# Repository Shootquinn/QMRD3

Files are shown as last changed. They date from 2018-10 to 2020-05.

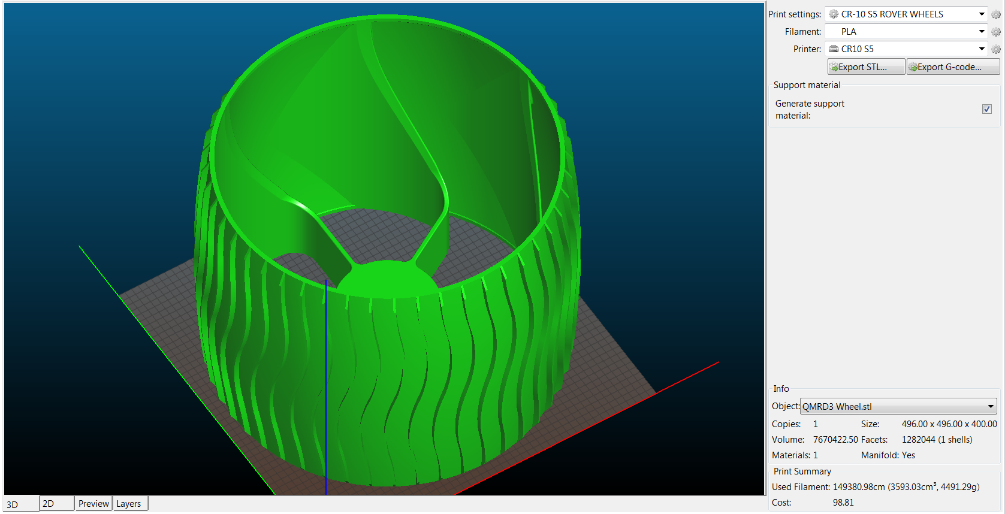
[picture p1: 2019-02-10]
QMRD3 Wheel Print Info Stock CR10S5.PNG

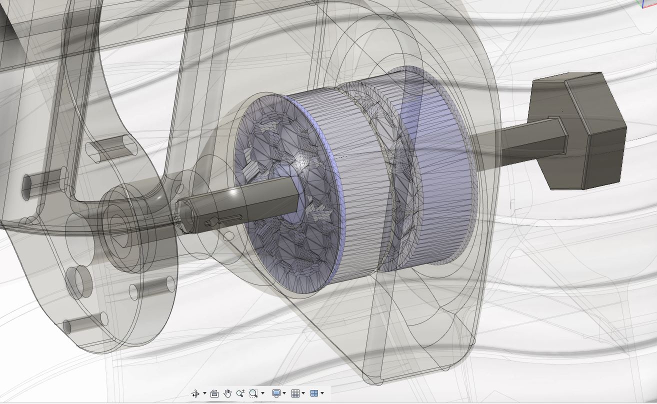
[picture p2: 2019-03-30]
QMRD3 Screenshot 2 - Wheel Bearings.JPG

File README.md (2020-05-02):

# QMRD3
Qualification Model Rover Demonstrator for Deep Drilling

Thanks to Roger-random, who created the amazing Sawppy rover on which this design is based.
      
This project is intended to be a testbed for future work on developing Mars ice drilling technologies. It would not be possible 
without the pioneering work by Github user Roger-random, who created the amazing Sawppy rover on which this rover is based. 
The Sawppy is a truly amazing and elegant design at an affordable price.

Unfortunately, this rover is not cheap. The wheels are around $100 each to print. 

The Rover Chassis has reached a release-ready state and all components have been prepared for the larger size. The drive motors are 
from makermotor and are available at: https://makermotor.com/pn00113-6-6-rpm-gear-motor-12vdc-high-torque/ 
while the steering motors are from Amazon seller STEPPERONLINE and can be found by searching for the following listing:
STEPPERONLINE 47:1 Planetary Gearbox Nema 23 Stepper Motor 2.8A. The mounting bracket for the stepper motor is required and will match up
to the bolt pattern on the steering corners. 

The electronics, etc. have not been designed yet. It would be nice to adapt the Ardupilot Rover but it may be difficult to run the steppers
in this configuration. One idea may be to have steering changes executed as macro code by the autopilot. As in, the rover moves to a way 
point, and when it is there it executes the macro at that way point to do a steering maneuver. 

You can find more about Roger's original Sawppy rover at https://hackaday.io/project/158208-sawppy-the-rover 
and https://github.com/Roger-random/Sawppy_Rover

Note: This rover uses the following bearing in 28+ locations: https://www.thingiverse.com/thing:3116838
      The bearing is a remix and therefore is released under a separate license and is maintained on Thingiverse. Two sizes are provided,
      88mm fits nicely when the bearing housings and printed with the diameter parallel to the xy plane, and the 87mm version fits nicely
      when the bearing housings are printed with the diameter perpendicular to or at odd angles to the xy plane. 
      Thanks to Zh4x0r for creating the parametric model with an integral lip, and thanks to Emmett for inventing 
      the gear bearing and completely changing the game.

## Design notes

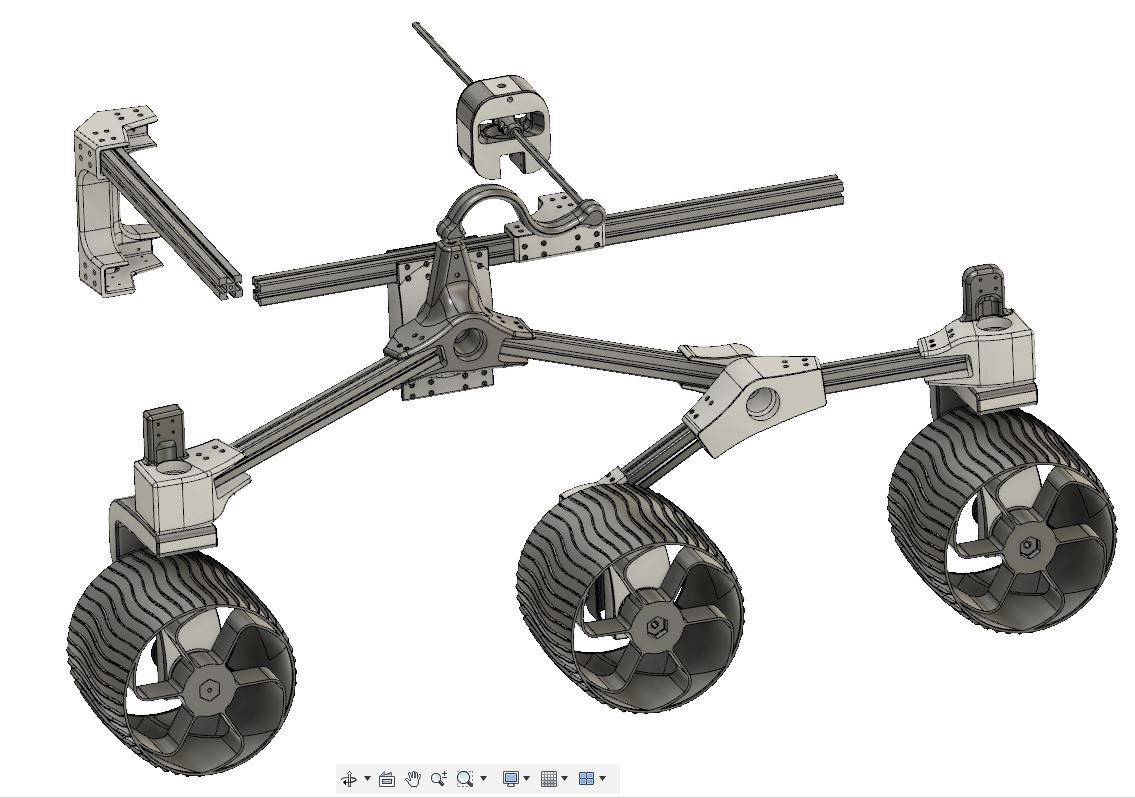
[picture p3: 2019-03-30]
QMRD3 Screenshot 1.JPG

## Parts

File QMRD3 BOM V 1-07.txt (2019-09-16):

QMRD3 BOM 6/24/19 v1.05

Printed Parts:

	Wheel, Axle, Couplers:
		Wheel  			6
		Axle 			14
		Drive Coupler 		6
		Steering Coupler 	4
		Bearing 		30
		Retainer Washer		4
		Thrust Washer 		22

	Left Rocker Bogie: 
		Steering Front Corner	1
		Steering Knuckle	2
		Rocker			1
		Steering Rear Corner	1
		Fixed Knuckle		1
		Bogie Rocker		1
		Bogie Pivot		1
	
	Right Rocker Bogie:
		Mirror all Left Rocker Bogie printed parts in your slicer.

	Body:
		Body Differential Bracket	1
		Body Differential Bracket Opp	1
		Body Suspension			2
		Body Corner			4

	Differential:
		Differential Body		1
		Differential Rocker-Link	1
		Differential Rocker-Link Opp	1
		Differential Swivel		1

	Optional Printed Parts:
		Axle Skinny (If, like me, you are over-extruding on wheel prints)
		Bearing 87mm (same logic as 'Axle Skinny,' but has good fit more frequently)
		Steering Lock-out Block (if using tank steering)
		Hexagon Hub Adapter for Aluminum Axles - NOT DESIGNED YET AS OF v1.07.

Extrusion - 30-6060 - (mm, inches, qty): 
1540	60.63		4
980	38.58		4
952	37.48		1
728	28.66		2
644	25.35		2
488	19.21		2
468	18.43		2

Aluminum Hexagon Bar - 5/8" / 16mm 6061-T6 Aluminum - (mm, inches, qty):
640	25.20		2
200	7.87		Optional Axle Stock

Motors
	Drive Motors:
		Makermotor PN00113-6, 12v, 21 Nm	6
	
	Steering Motors:
		NEMA 23 w/46.656:1, 24v, 40 Nm		4
		(Get angle the bracket for it too)

Screws and Inserts
	Fastener		Qty	Quantity can vary, not every fastener hole needs to be used.
	M6 T-slot nuts:		100+	Roll-in with Spring Ball highly recommended. Get the one for 3030!
	M6 Screw 10mm		32+
	M6 Screw 16mm		32+
	M6 Screw 20mm		32+
	M6 Screw 25mm		24+
	M6 Screw 30mm		12	Optional, may be needed in a few places
	M6 Heat-set inserts	30	Long type
	M4 Screws		24	Assorted Lengths 8mm - 20mm
	M4 Heat-set Inserts	24	20 Long and 4 short

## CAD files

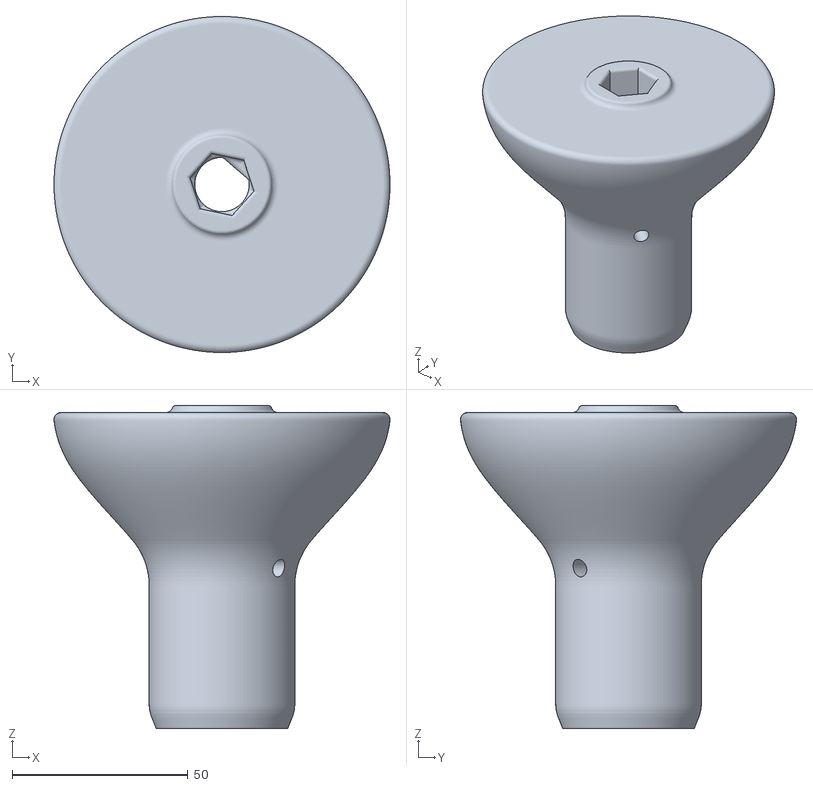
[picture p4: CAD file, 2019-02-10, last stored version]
QMRD3 Drive Coupler.stl
95.7 x 95.7 x 92.0

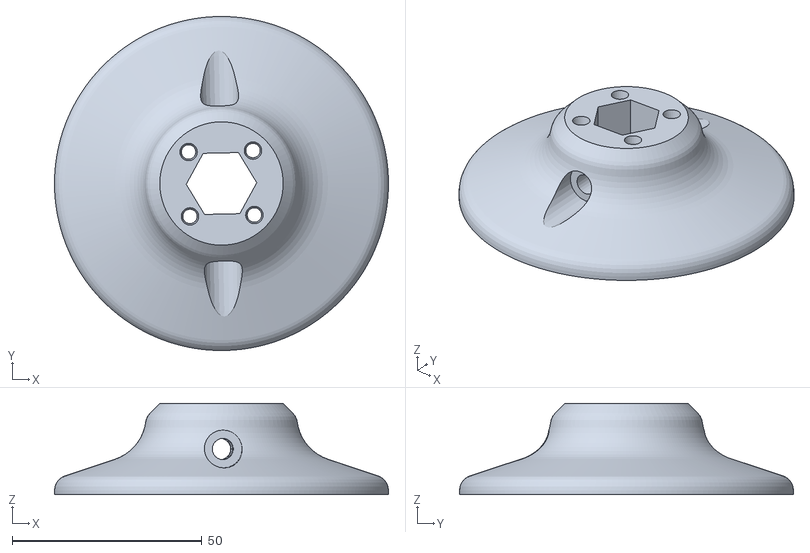
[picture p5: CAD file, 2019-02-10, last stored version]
QMRD3 Steering Coupler.stl
88.0 x 88.0 x 24.0

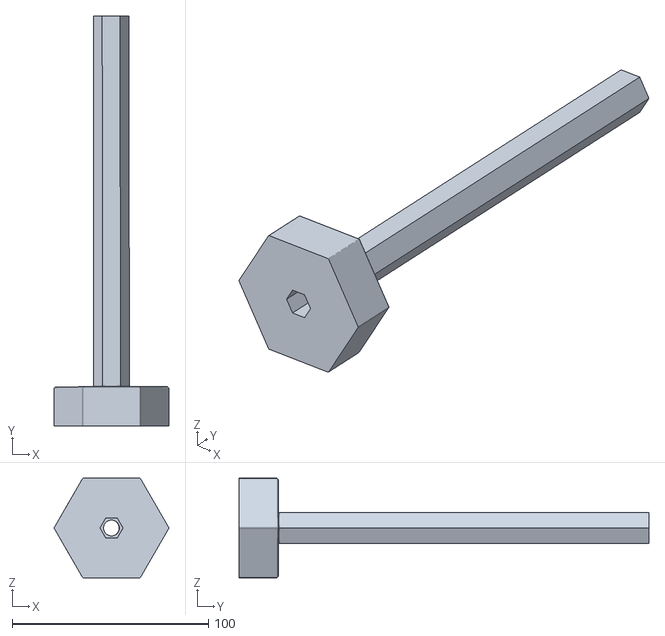
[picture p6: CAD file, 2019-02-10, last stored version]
QMRD3 Axle.stl
58.5 x 209.0 x 50.8

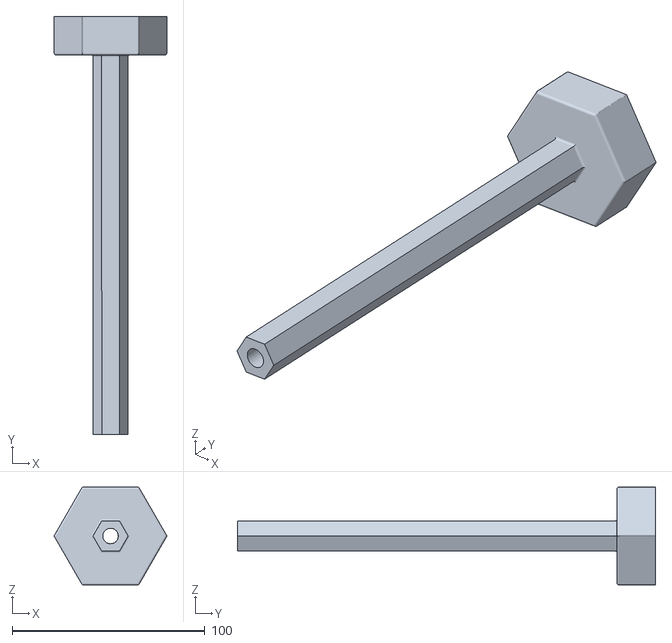
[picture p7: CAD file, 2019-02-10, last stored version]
QMRD3 Axle New.stl
58.5 x 217.0 x 50.8

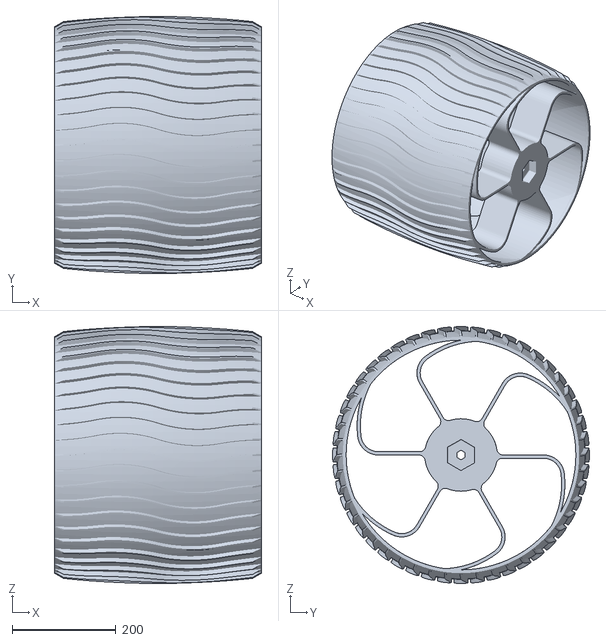
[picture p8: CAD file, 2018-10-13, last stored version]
QMRD3 Wheel Decimated.stl
400.0 x 496.0 x 496.0

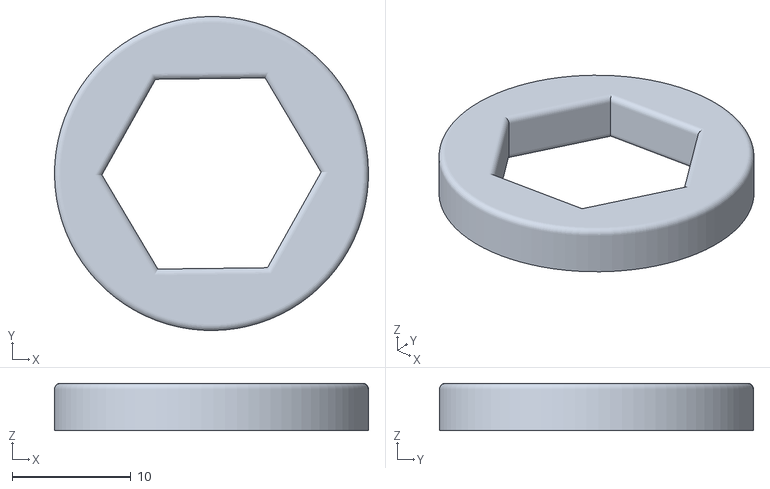
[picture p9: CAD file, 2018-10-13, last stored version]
QMRD3 Thrust Washer.stl
26.5 x 26.5 x 4.00

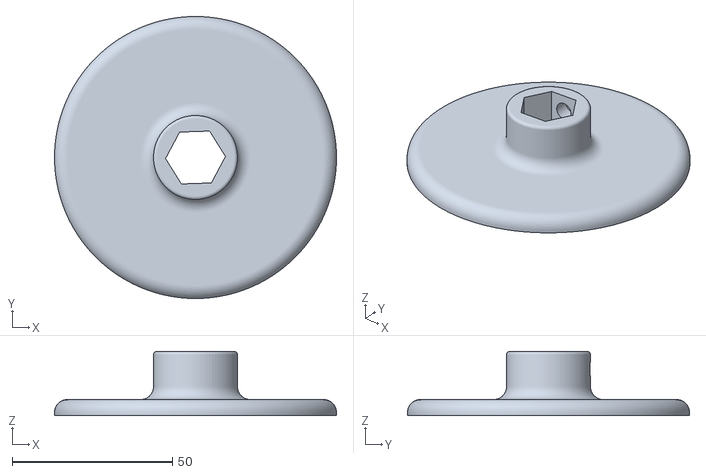
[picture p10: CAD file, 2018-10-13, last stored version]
QMRD3 Retainer Washer.stl
88.0 x 88.0 x 20.0

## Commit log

2018-10-22 Updated axle model, polygons were not aligned
    [QMRD3 Axle.stl]
2018-10-22 Fixed axle, polygons were not aligned.
2018-10-22 Add files via upload
    Rotated Axle STL
    [QMRD3 Axle.stl]
2018-10-22 Add files via upload
    Motor Mount Updated
2019-03-24 Fusion Archive, Version 1.00 of QMRD3
    Not all parts have been printed yet. Expect future changes and mistakes. STLs on Git do not yet comply with Version 1 Fusion archive.
2019-03-30 V 1.02 STLs
    STLs are provided in 4 separate zip files and all comply with V 1.02. The wheel is left in the root directory for in-browser viewing.
2019-04-12 1.03 STLs
    Steering knuckle updated to facilitate plastic axle install (for steering corner).
2019-06-17 1.05
    Wheel with larger hex for axle shaft (easier fittings due to seams etc on wheel), fixed front corner STL (was actually a knuckle), added skinny axle to help with tight wheel holes.
